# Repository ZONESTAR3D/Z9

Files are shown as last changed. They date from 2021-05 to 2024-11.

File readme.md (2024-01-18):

### :globe_with_meridians: Choose Language (Translated by google)
(https://github-com.translate.goog/ZONESTAR3D/Z9?_x_tr_sl=en&_x_tr_tl=es)
(https://github-com.translate.goog/ZONESTAR3D/Z9?_x_tr_sl=en&_x_tr_tl=pt)
(https://github-com.translate.goog/ZONESTAR3D/Z9?_x_tr_sl=en&_x_tr_tl=fr)
(https://github-com.translate.goog/ZONESTAR3D/Z9?_x_tr_sl=en&_x_tr_tl=de)
(https://github-com.translate.goog/ZONESTAR3D/Z9?_x_tr_sl=en&_x_tr_tl=it)
(https://github-com.translate.goog/ZONESTAR3D/Z9?_x_tr_sl=en&_x_tr_tl=sv)
(https://github-com.translate.goog/ZONESTAR3D/Z9?_x_tr_sl=en&_x_tr_tl=pl)
(https://github-com.translate.goog/ZONESTAR3D/Z9?_x_tr_sl=en&_x_tr_tl=da)
(https://github-com.translate.goog/ZONESTAR3D/Z9?_x_tr_sl=en&_x_tr_tl=cs)
(https://github-com.translate.goog/ZONESTAR3D/Z9?_x_tr_sl=en&_x_tr_tl=hr)
(https://github-com.translate.goog/ZONESTAR3D/Z9?_x_tr_sl=en&_x_tr_tl=ro)
(https://github-com.translate.goog/ZONESTAR3D/Z9?_x_tr_sl=en&_x_tr_tl=sk)

(https://github-com.translate.goog/ZONESTAR3D/Z9?_x_tr_sl=en&_x_tr_tl=ru)
(https://github-com.translate.goog/ZONESTAR3D/Z9?_x_tr_sl=en&_x_tr_tl=ja)
(https://github-com.translate.goog/ZONESTAR3D/Z9?_x_tr_sl=en&_x_tr_tl=ko)
(https://github-com.translate.goog/ZONESTAR3D/Z9?_x_tr_sl=en&_x_tr_tl=id)
(https://github-com.translate.goog/ZONESTAR3D/Z9?_x_tr_sl=en&_x_tr_tl=th)
(https://github-com.translate.goog/ZONESTAR3D/Z9?_x_tr_sl=en&_x_tr_tl=vi)
(https://github-com.translate.goog/ZONESTAR3D/Z9?_x_tr_sl=en&_x_tr_tl=iw)
(https://github-com.translate.goog/ZONESTAR3D/Z9?_x_tr_sl=en&_x_tr_tl=ar)
(https://github-com.translate.goog/ZONESTAR3D/Z9?_x_tr_sl=en&_x_tr_tl=tr)
(https://github-com.translate.goog/ZONESTAR3D/Z9?_x_tr_sl=en&_x_tr_tl=el)
(https://github-com.translate.goog/ZONESTAR3D/Z9?_x_tr_sl=en&_x_tr_tl=pt)
(https://github-com.translate.goog/ZONESTAR3D/Z9?_x_tr_sl=en&_x_tr_tl=zh-CN)

----
### About ZONESTAR Z9 series 3d printer
The main features of Z9 include:  
1. Used **Aluminum profile frame** structure makes the machine  stronger and more stable. The profiles screw is directly fixed, which is more accurate than using profile connectors.  
2. Used **Core-XY** drive structure effectively reduces the weight of the motion system.
3. Used **Open builds pulley + V-profile track**. It has the comprehensive characteristics of high precision, high speed, low resistance and low cost.  
4. **Dule drive z-axis** design is adopted to simplify leveling and improve the stability of the printing platform.  
5. **Elastic replaceable hotend** design is adopted. Fast heat exchange end (extruder) can be selected according to different printing material requirements.   More details, please refer to [**here**](https://github.com/ZONESTAR3D/Upgrade-kit-guide/tree/main/HOTEND)

----
## :file_folder:[Z9V5](https://github.com/ZONESTAR3D/Z9/tree/main/Z9V5)
**Z9V5** is the latest version of Z9 series. Compared with **Z9M4**, the main upgrades include:  
1. Higher pre assembly ratio and faster installation.  
2. The appearance is more beautiful.  
3. Using TMC silent motor drive module, the operation noise is lower (less than 55db @ 1 meter distance).  
4. Upgrade to dual Z driver.  
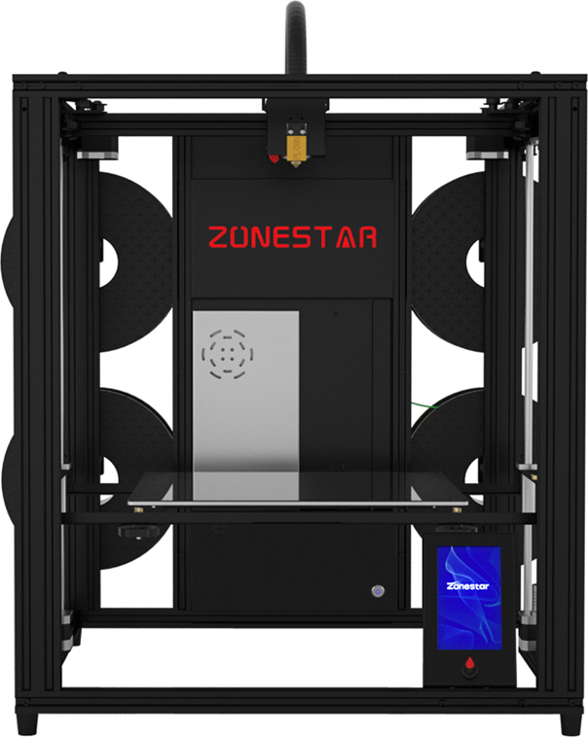
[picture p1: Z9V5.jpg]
Z9V5

#### What's different between Z9V5 with Z9V5Pro    
1. **Z9V5** used 128x64 dots LCD screen (LCD12864) and a PC hotbed film.  
2. **Z9V5Pro** used used a 4.3" TFT-LCD screen (LCD-DWIN) and glass print platform.
  
### [:file_folder:Z9V5-MK1](https://github.com/ZONESTAR3D/Z9/tree/main/Z9V5/Z9V5-MK1) 
**The first version Z9V5**.   

### [:file_folder:Z9V5-MK2](https://github.com/ZONESTAR3D/Z9/tree/main/Z9V5/Z9V5-MK2)
**The 2nd version Z9V5**.   
##### Z9V5-MK2 upgrade than Z9V5-MK1:  
1. **Hot end interface** When shipping, the print head (hotend assembly) is separated from the backplane. There are 5 connectors behind the backplane, which can connect the wiring of the hot end without opening the control box. It will help switch between [**different types of hotends**](https://github.com/ZONESTAR3D/Upgrade-kit-guide/tree/main/HOTEND) quickly.  
2. Improved the M4 hotend from the 2nd version (HM4-V2) to the 3rd version(HM4-V3). More details of the M4 hotend, please refer to [Here](https://github.com/ZONESTAR3D/Upgrade-kit-guide/tree/main/HOTEND/M4%20%204-IN-1-OUT%20Mixing%20Color%20Hotend).  
3. Improved the backlight of ZONESTAR LOGO.  
4. Improved the cover case of control box to make it easier to open.  
5. improved the belt transmission device to prevent the belt from scratching the idler pulley.  
6. improved the filament run out installation to make it solve the problem that may lead to the winding of filament.    
    
### [:file_folder:Z9V5-MK3](https://github.com/ZONESTAR3D/Z9/tree/main/Z9V5/Z9V5-MK3)
**The 3rd version Z9V5**.    
##### **Z9V5-MK3 mainly improves than Z9V5-MK2**:  
1. Upgraded bed leveling sensor to [**ZLSensor**](https://aliexpress.com/item/1005002865311470.html), to replace the PL-08N bed leveling sensor. ZLSensor can probing the glass directly.  
2. Upgraded the extruder motor drivers to [**TMC2225**](https://aliexpress.com/item/1005003270721219.html)(from A4988). So **Z9V5-MK3**'s firmware is different with **Z9V5-MK1** and **Z9V5-MK2**.  

### [:file_folder:Z9V5-MK4](https://github.com/ZONESTAR3D/Z9/tree/main/Z9V5/Z9V5-MK4)
**The 4th version Z9V5**.    
##### **Z9V5-MK4 mainly improves than Z9V5-MK3**:  
1. Use 4-IN-1-OUT non color mixing hotend as default hotend.
2. Use magnetic hot bed sticker to replace hot bed glass.
3. Bed leveling sensor used PL-08N.
4. Optimized structure on top assembly, filament run out sensor case.

### [:file_folder:Z9V5-MK5](https://github.com/ZONESTAR3D/Z9/tree/main/Z9V5/Z9V5-MK5)
**The 5th version Z9V5**.    
##### **Z9V5-MK5 mainly improves than Z9V5-MK4**:  
Used M4V6 (the 6th version 4-IN-1-OUT mix color) hotend as default hotend to replace of the E4 hotend.   

### [:file_folder:Z9V5-MK6](https://github.com/ZONESTAR3D/Z9/tree/main/Z9V5/Z9V5-MK6)
**The 6th version Z9V5**.    
##### **Z9V5-MK6 mainly improves than Z9V5-MK5**:  
1. Upgrade to Dual Gear Extruders (2x BMG left hand and 2x BMG right hand).
2. Upgrade control board to ZM3E4 V3.0.1.    
3. Changed the motor drive modules (4xTMC2208 + 4xA4988).

----
## :file_folder:[Z9M4](./Z9M4/) 
#### [:book:Documents](./Z9M4/readme.md)    
**Z9M4** is a version of Z9 series launched in 2020. Compared with Z9FM3, the main upgrades include:  
1. Upgrade to 4 extruders  
2. Upgrade to 4-IN-1-OUT hotend  
3. Upgrade to 32 bits control board  
**NOTE: Z9M4 is stopped produce since April 2021**  
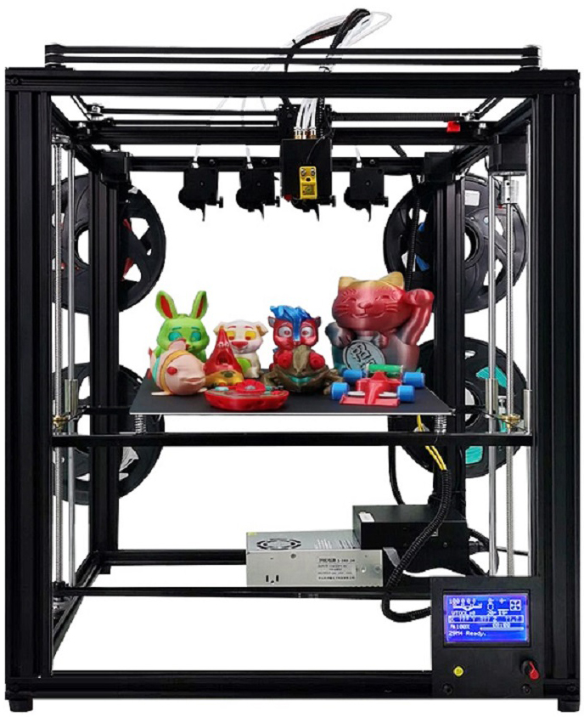
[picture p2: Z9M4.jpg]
Z9M4


----
## :file_folder:[Z9M3](./Z9M4/)  
**Z9M3** is a version of Z9 series launched in 2019.  it has produced two versions, Z9T/Z9F. Compared with Z9M2, the main upgrades include:  
1. Upgrade to 3 extruders  
2. Upgrade to 3-IN-1-OUT hotend  
3. From Z9F, it upgrade the extduer to a Titan extruders.  
**NOTE: Z9M3 is stopped produce since April 2020**  
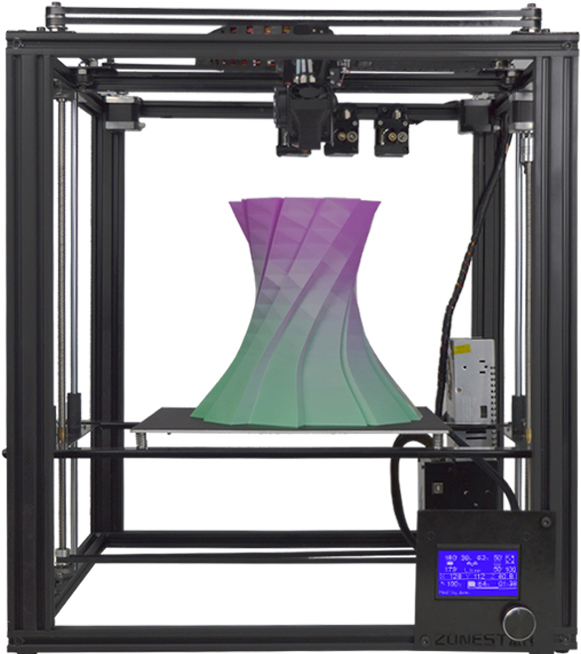
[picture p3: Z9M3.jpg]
Z9FM3
  

----
## Z9M2 
**Z9M2** launched in 2018, it is the first verison of Z9 series. it has produced two versions, Z9 and Z9S. Z9 use a H-BOT structure and Z9S used a Core-XY structure, and after Z9S, all of the Z9 series are used Core-XY structure.

------
### :memo: How to downlod files from Github page?
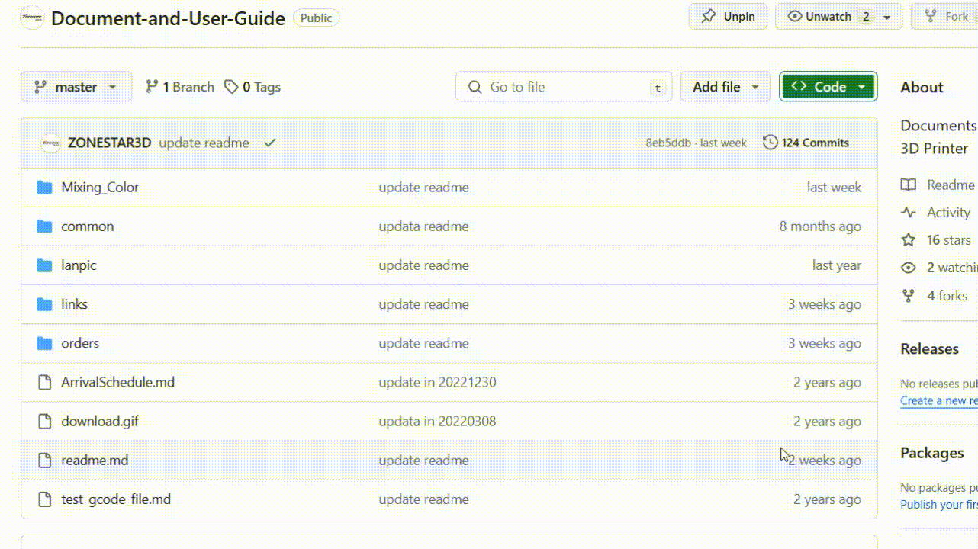
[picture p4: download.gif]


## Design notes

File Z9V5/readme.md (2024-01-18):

# User Guide for ZONESTAR Z9V5 3D Printer 

-----
## Contents
- **[Translate this page](#translate-this-page)**
- **[User Guide links](#link-to-user-guide-for-z9v5pro-3d-printers)**
- **[What's different on Z9V5-MK1/MK2/MK3/MK4/MK5/MK6](#whats-different-on-z9v5-mk1mk2mk3mk4mk5mk6)**
- **[How to distinguish Z9V5-MK1/MK2/MK3/MK4/MK5/MK6](#how-to-distinguish-z9v5-mk1mk2mk3mk4mk5mk6)**
- **[Troubleshooting](#troubleshooting)**

-----
### :globe_with_meridians: Translate this page
We provide online documentation because it is easily translated into a language you are familiar with. Here are some common browser translation plug-ins for your reference.
- [**Windows Edge Translate Add-on**](https://microsoftedge.microsoft.com/addons/detail/edge-translate/bfdogplmndidlpjfhoijckpakkdjkkil?hl=en-US)    
- [**Firefox Translations Add-on**](https://support.mozilla.org/en-US/kb/firefox-translations-add-on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)
- [**Google Translate Chrome Extension**](https://chrome.google.com/webstore/detail/google-translate/aapbdbdomjkkjkaonfhkkikfgjllcleb)

-----
### Link to user guide for Z9V5Pro 3D Printers 
- :file_folder: **Z9V5Pro-MK6: https://github.com/ZONESTAR3D/Z9/tree/main/Z9V5/Z9V5-MK6**    
- :file_folder: **Z9V5Pro-MK5: https://github.com/ZONESTAR3D/Z9/tree/main/Z9V5/Z9V5-MK5**    
- :file_folder: **Z9V5Pro-MK4: https://github.com/ZONESTAR3D/Z9/tree/main/Z9V5/Z9V5-MK4**    
- :file_folder: **Z9V5Pro-MK3: https://github.com/ZONESTAR3D/Z9/tree/main/Z9V5/Z9V5-MK3**    
- :file_folder: **Z9V5Pro-MK2: https://github.com/ZONESTAR3D/Z9/tree/main/Z9V5/Z9V5-MK2**    
- :file_folder: **Z9V5Pro-MK1: https://github.com/ZONESTAR3D/Z9/tree/main/Z9V5/Z9V5-MK1**    

-----
### What's different on Z9V5-MK1/MK2/MK3/MK4/MK5/MK6
#### :black_circle: Z9V5-MK6 mainly improves than Z9V5-MK5:       
1. Upgraded to Dual Gear Extruders.
2. Upgraded control board to ZM3E4 V3.     
3. Changed motor drivers: TMC2208 used on driving XYZ motors and A4988 used on driving extrurder motors.     
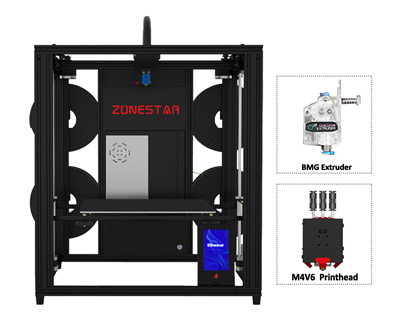
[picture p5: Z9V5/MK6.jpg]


#### :black_circle: Z9V5-MK5 mainly improves than Z9V5-MK4:     
Used M4V6 (the 6th version 4-IN-1-OUT mix color) hotend as default hotend.   
**[What's different between M4V6 hotend and E4 hotend][FAQ_M4E4].**     
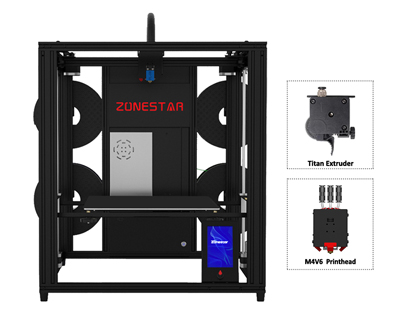
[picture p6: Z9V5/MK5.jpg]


#### :black_circle: Z9V5-MK4 mainly improves than Z9V5-MK3:  
1. Use E4 (4-IN-1-OUT non mix color) hotend as default hotend.
2. Use flexibel magnetic hot bed sticker to replace hot bed glass.
3. Bed leveling sensor used PL-08N.
4. Optimized structure on top assembly, filament run out sensor case, etc..    
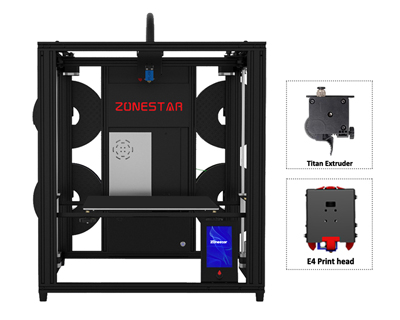
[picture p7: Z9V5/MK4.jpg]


#### :black_circle: Z9V5-MK3 mainly improves than Z9V5-MK2:
1. Upgraded bed leveling sensor to [**ZLSensor**](https://aliexpress.com/item/1005002865311470.html) from [**PL-08N**](https://www.aliexpress.com/item/2255800409994958.html), ZL-Sensor can probing the glass directly.  
2. Changed motor drivers: TMC2225 used on driving XYZ motors and extrurder motors..     
3. Upgraded the M4 hotend from the 3nd version (***M4V3***) to the 4th version(***M4V4***).      
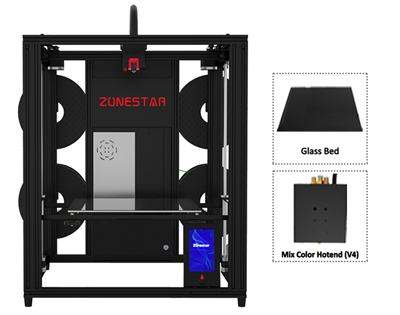
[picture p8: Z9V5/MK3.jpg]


#### :black_circle: Z9V5-MK2 mainly improves than Z9V5-MK1:    
1. Added air connectors for hot end wiring, making it easier to switch between different types of hot ends.
2. Upgraded the M4 hotend from the 2nd version (***M4V2***) to the 3rd version(***M4V3***). .  
3. Improved the backlight of ZONESTAR LOGO.  
4. Improved the cover case of control box to make it easier to open.  
5. improved the belt transmission device to prevent the belt from scratching the idler pulley.  
6. improved the filament run out installation.    
:warning: **NOTE** :warning:   
Due to the shortage of chips, a small numbers of **Z9V5-MK2** used **ZM3E4V1** control board. Please check the product serial number (a white lable pasted on the power supply). If the product with serial number **V1xxxxxxxx** , it means your machine used a **ZM3E4V1** control board. Basically ZM3E4V1 has the same features with ZM3E4V2.        
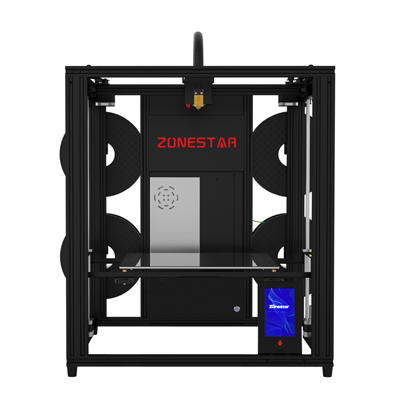
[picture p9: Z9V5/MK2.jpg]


#### :black_circle: Z9V5-MK1 is the first version Z9V5    

-----
### How to distinguish Z9V5-MK1/MK2/MK3/MK4/MK5/MK6
You can distinguish MK1/MK2/MK3/MK4 by product serial number. There is a white sticker on the power supply, which indicates the product serial number.  

- **Z9V5-MK1:** Serial Number is **xxxxxxxxxx**   
- **Z9V5-MK2:** Serial Number is **V1-xxxxxxxxxx** and **V2-xxxxxxxxxx**    
- **Z9V5-MK3:** Serial Number is **MK3-xxxxxxxxxx**  
- **Z9V5-MK4:** Serial Number is **MK4-xxxxxxxxxx**  
- **Z9V5-MK5:** Serial Number is **MK5-xxxxxxxxxx**  
- **Z9V5-MK6:** Serial Number is **MK6-xxxxxxxxxx**  

-----
### Troubleshooting
If you have any problem when installing and using Z9V5, please read the [**:book: Z9V5Pro Troubleshooting**][Troubleshooting] to find a solution a solution first.

-----
### :memo: How to downlod files from Github page?
   

-----
[FAQ_M4E4]: https://github.com/ZONESTAR3D/Upgrade-kit-guide/blob/main/HOTEND/FAQ_M4E4.md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
[Troubleshooting]: https://github.com/ZONESTAR3D/Z9/tree/main/Z9V5/Z9V5_FAQ

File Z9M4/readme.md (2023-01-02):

### :globe_with_meridians: Choose Language (Translated by google)
(https://github-com.translate.goog/ZONESTAR3D/Z9/tree/main/Z9M4?_x_tr_sl=en&_x_tr_tl=es)
(https://github-com.translate.goog/ZONESTAR3D/Z9/tree/main/Z9M4?_x_tr_sl=en&_x_tr_tl=fr)
(https://github-com.translate.goog/ZONESTAR3D/Z9/tree/main/Z9M4?_x_tr_sl=en&_x_tr_tl=pt)
(https://github-com.translate.goog/ZONESTAR3D/Z9/tree/main/Z9M4?_x_tr_sl=en&_x_tr_tl=de)
(https://github-com.translate.goog/ZONESTAR3D/Z9/tree/main/Z9M4?_x_tr_sl=en&_x_tr_tl=it)
(https://github-com.translate.goog/ZONESTAR3D/Z9/tree/main/Z9M4?_x_tr_sl=en&_x_tr_tl=pl)
(https://github-com.translate.goog/ZONESTAR3D/Z9/tree/main/Z9M4?_x_tr_sl=en&_x_tr_tl=ru)
(https://github-com.translate.goog/ZONESTAR3D/Z9/tree/main/Z9M4?_x_tr_sl=en&_x_tr_tl=pt)
(https://github-com.translate.goog/ZONESTAR3D/Z9/tree/main/Z9M4?_x_tr_sl=en&_x_tr_tl=el)

(https://github-com.translate.goog/ZONESTAR3D/Z9/tree/main/Z9M4?_x_tr_sl=en&_x_tr_tl=ja)
(https://github-com.translate.goog/ZONESTAR3D/Z9/tree/main/Z9M4?_x_tr_sl=en&_x_tr_tl=ko)
(https://github-com.translate.goog/ZONESTAR3D/Z9/tree/main/Z9M4?_x_tr_sl=en&_x_tr_tl=id)
(https://github-com.translate.goog/ZONESTAR3D/Z9/tree/main/Z9M4?_x_tr_sl=en&_x_tr_tl=th)
(https://github-com.translate.goog/ZONESTAR3D/Z9/tree/main/Z9M4?_x_tr_sl=en&_x_tr_tl=vi)
(https://github-com.translate.goog/ZONESTAR3D/Z9/tree/main/Z9M4?_x_tr_sl=en&_x_tr_tl=iw)
(https://github-com.translate.goog/ZONESTAR3D/Z9/tree/main/Z9M4?_x_tr_sl=en&_x_tr_tl=ar)
(https://github-com.translate.goog/ZONESTAR3D/Z9/tree/main/Z9M4?_x_tr_sl=en&_x_tr_tl=tr)
(https://github-com.translate.goog/ZONESTAR3D/Z9/tree/main/Z9M4?_x_tr_sl=en&_x_tr_tl=zh-CN)
----------
## NOTICE
### Before using the 3d printer, please:  
1. Carefully to read the pages (from 54~56) in the "1. User Guide\Z9M4 user guide".  
2. Carefully to read the file "1. User Guide\Mix Color HOTEND User Guide - load and unload filament.pdf".  
3. Carefully to read "1. User Guide\Operature guide for Mixing Color Printer.pdf"  
***ATTETION: Incorrect filament loading may cause to clog the hotend, if the hotend is clogged, please refer to the document "4. TroubleShootings\How to clean the cloged mixing color hotend.pdf" to fix***  

## Download Z9M4 files
[**Download all the Z9M4 files in one go**](https://downgit.github.io/#/home?url=https:%2F%2Fgithub.com%2FZONESTAR3D%2FZ9%2Ftree%2Fmain%2FZ9M4)     
**If it doesn't work, please refer to** [**here**](https://stackoverflow.com/questions/7106012/download-a-single-folder-or-directory-from-a-github-repo)     
   
# Documents
## 1. User Guide 
**Included:**  
1. Installation and quick user guide  
2. LCD screen menu description  
3. Installation video tutorial  
4. Operature guide for mixing color printer    

## 2. Operation Guide
**Included:**  
1. USB driver  
2. Host Software - Print from PC guide  
3. Advanced features guide  
4. Bed auto leveling feature guide  

## 3. Slicing
**Included slicing guide, for the newest slicing guide, please click here [slicing guide](https://github.com/ZONESTAR3D/Slicing-Guide)**

## 4. Test gcode
**Included some testing gcode files**  

## 5. TroubleShootings
**Included troubleshooting and FAQ files**

## 6. Print Parts
**Parts stl files for this kit**   

## 7. Firmware
- [**Firmware bin file**](https://github.com/ZONESTAR3D/Firmware/tree/master/Z9/Z9M4)  
- [**Firmware source code** ](https://github.com/ZONESTAR3D/source-code-for-3d-printer)

## Video tutorial  
**NOTE: The video tutorial may be a little different with your machine because of firmware version is different, for reference only**     
### Installation and operation      
- [***How to load filament (one color)***](https://youtu.be/W1_XiT4g9kg)  
- [***How to load filament (Mutli-colors)***](https://youtu.be/Rsd8GYrEVCQ)  
- [***Bed Leveling***](https://youtu.be/lgYZA-pzMsM)    
- [***Gradient Mixing Color Printing***](https://youtu.be/agj3J1HBDt8)    
- [***Random Mixing Color Printing***](https://youtu.be/qvT_BX4C2Rk)  

### Advanced features
- [***Auto Retract Feature***](https://youtu.be/4HVIGxZfM80)  
- [***Filament Runout***](https://youtu.be/viTvzIskwY8)  

### Slicing guide (by Cura)  
- [***Install and setup Cura***](https://youtu.be/h2GynyUo7wQ)    
- [***slicing 1 color 3d object***](https://youtu.be/UDgjGRFrELc)    
- [***slicing 4 colors 3d object***](https://youtu.be/hP6Socp-Cz0)     
- [***slicing 8 colors 3d object***](https://youtu.be/qQ6UnTysqK0)          

# Z9 upgrade kit / parts
## Laser engine
By upgrading this item, you can turn your 3D printer into a simple laser engraving machine. Higher power laser modules can improve engraving speed or support materials with higher melting point.  
- [**User guide**](https://github.com/ZONESTAR3D/Upgrade-kit-guide/tree/main/Laser%20Engraving)  
- [**Sell link**](https://www.aliexpress.com/item/4001309902136.html)  
## WiFi
By upgrading this item, you can remote control your 3d printer.    
- [**User guide**](https://github.com/ZONESTAR3D/Upgrade-kit-guide/tree/main/WiFi)  
- [**Sell link**](https://www.aliexpress.com/item/1005002378551489.html)  
## Direct drive extruder
By upgrading this project, you can print flexible materials (such as TPU filament). Of course, it also has other advantages and disadvantages of the "direct drive" extruders, such as having less strings issue, better flow, more supporting materials, etc., Also because of the heavier weight of the extruder, the printing speed must be lower.  
- [**User guide**](https://github.com/ZONESTAR3D/Upgrade-kit-guide/tree/main/Direct%20Drive%20Extrruder)   
- [**Sell link**](https://www.aliexpress.com/item/1005002847644867.html)   
## Hotends
Each type of hot end has its advantages and disadvantages, you can choose different hotends according to different requirement:    
- **High-speed and high-temperature Hotend (single color)**: It can support higher  printing speed and higher temperature consumables (up to 300 degrees when using stainless steel nozzles), and can be used to print PVC and PC.  
- **3-IN-3-OUT Hotend**: It can support printing different typs of filaments in one 3d prints, such as PLA+PVA.  
- **3-IN-2-OUT Hotend**: It can be regarded as a combination of 2-IN-1-OUT and a single-color hot end, which can simultaneously achieve the needs of color mixing and printing of different materials.    
We will launch more hot ends in the future, so stay tuned. If you have any suggestions, please don't hesitate to let us know at any time.   
- [**User guide**](https://github.com/ZONESTAR3D/Upgrade-kit-guide/tree/main/HOTEND)   
- [**4-IN-1-OUT Non-Mixing hotend**](https://www.aliexpress.com/item/1005002951777699.html)   
- [**High Speed Printing hotend**](https://www.aliexpress.com/item/1005002829919346.html)  
- [**3-IN-1-OUT hotend**](https://www.aliexpress.com/item/1005001275429959.html)
- [**3-IN-2-OUT hotend**](https://www.aliexpress.com/item/1005001275429959.html)
- [**3-IN-3-OUT hotend**](https://www.aliexpress.com/item/1005001275429959.html)
## Bed leveling sensor
- [**User guide**](https://github.com/ZONESTAR3D/Upgrade-kit-guide/tree/main/Bed%20Leveling%20Sensor)    
- [**ZLSensor**](https://www.aliexpress.com/item/1005002865311470.html)  
- [**3DTouch**](https://www.aliexpress.com/item/1005001464420529.html)

## How to downlod files from Github page
#### Step 1: Click this link [**https://downgit.github.io/**](https://downgit.github.io/) 
#### Step 2: Copy the Github file or direcotry link which you want to download.
#### Step 3: Click download button and wait a few seconds, it will start to download automatically. 


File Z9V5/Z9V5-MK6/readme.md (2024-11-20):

[M4V6_PRECAUTION]: https://github.com/ZONESTAR3D/Upgrade-kit-guide/blob/main/HOTEND/M4/M4_V6/M4V6_Precaution.md
[Z9V5MK6_STEPBYSTEP]: https://github.com/ZONESTAR3D/Z9/blob/main/Z9V5/Z9V5-MK6/step_by_step.md
[Z9V5MK6_LOADFILAMENT]: https://github.com/ZONESTAR3D/Z9/blob/main/Z9V5/Z9V5-MK6/2.Operation/Operation.md#load-filaments
[Z9V5MK6_OPTION]: https://github.com/ZONESTAR3D/Z9/blob/main/Z9V5/Z9V5-MK6/OptionalFeatures.md
[LINK_M4V6]: https://github.com/ZONESTAR3D/Upgrade-kit-guide/blob/main/HOTEND/M4/M4_V6
[LINK_MIX_FEATURE]: https://github.com/ZONESTAR3D/Document-and-User-Guide/blob/master/Mixing_Color
[LINK_FIRMWARE]: https://github.com/ZONESTAR3D/Firmware/blob/master/Z9/Z9V5/bin/Z9V5Pro-MK6
[LINK_SOURCECODE]: https://github.com/ZONESTAR3D/source-code-for-3d-printer
[LINK_TROUBLESHOOTING]: https://github.com/ZONESTAR3D/Z9/blob/main/Z9V5/Z9V5_FAQ
[M4_TEST_GCODE]: https://github.com/ZONESTAR3D/Slicing-Guide/blob/master/PrusaSlicer/test_gcode/M4/readme.md
[GCODE_REF1]: https://beginner3dprinting.com/what-is-g-code-in-3d-printing/
[GCODE_REF2]: https://www.reprap.org/wiki/G-code

----
## <a id="choose-language">:globe_with_meridians: Choose language </a>










----
# User Guide for ZONESTAR Z9V5Pro-MK6 3D Printer 
### [:arrow_down: Download All Document](https://downgit.github.io/#/home?url=https://github.com/ZONESTAR3D/Z9/tree/main/Z9V5/FZ9V5-MK6) 

----
## :warning: ATTENTION PLEASE
#### :loudspeaker: Before using the machine, please read [:book:"Precautions for using M4V6"][M4V6_PRECAUTION] carefully.
#### :loudspeaker: Must load 4 filaments onto the M4V6 hotend simultaneously, incorrect operationa may block the mix color hotend. If the hot end blockage caused by incorrect operation, it is not covered by the warranty. For how to load filaments, please refer to [:book: this guide][Z9V5MK6_LOADFILAMENT].
#### :loudspeaker: If you are a beginner of 3d printer, please carefully read the [:book: Step-by-Step Guide][Z9V5MK6_STEPBYSTEP], and following the steps to do.   
- [:book: **Precautions for using M4V6**][M4V6_PRECAUTION]
- [:book: **How to load filaments correctly**][Z9V5MK6_LOADFILAMENT]
- [:book: **Step-by-Step Guide**][Z9V5MK6_STEPBYSTEP] 

------
## :book: Contents
- [**Installation guide**](#a1)  
- [**Operation guide**](#a2)  
- [**Test gcode files**](#a3)
- [**Slicing software**](#a4)
- [**Firmware**](#a5)
- [**Troubleshootings**](#a6)
- [**Print parts stl files**](#a7)
- [**Optional upgrade features**](#a8)

-----
## <a id="a1"> 1. Installation guide </a>
First, please refer to the following documents and videos to complete the installation and wiring of the machine.
### Installation   
- [:book: Installation Guide Online Document](./1.Installation/Installation.md) 
- [:blue_book: Installation Guide PDF file](./1.Installation/Installation.pdf) 
- [:clapper: Installation Guide Video tutorial](https://youtu.be/TGHUVzV1Pg4)   
### Wiring    
- [:book: Wiring Guide Online Document](./1.Installation/Wiring.md) 
- [:blue_book: Wiring Guide PDF file](./1.Installation/Wiring.pdf) 
- [:art: Wiring diagram](./1.Installation/Z9V5Pro_Wiring_Diagram.jpg) 
- [:clapper: Wiring Video tutorial](https://youtu.be/tQQNLDOpdQU)

## <a id="a2"> 2. Operation Guide </a>
### **Introduction to LCD Control Panel**     
After completing the installation and wiring, please take a look the below guide to know how to use the control panel (LCD Screen), and understand the functions of LCD menu generally.      
- [:book: LCD Menu Online Document](./2.Operation/LCDMENU_Description.md)    
- [:blue_book: LCD Menu PDF file](./2.Operation/LCDMENU_Description.pdf)    
#### **Print your first works**     
Now you can try to print your "Hello word" works, before starting printing, you first need to make a simple correction to the height of the hot bed (it is called "bed leveling"), and then load the filaments into the extruder (please note that regardless of the color of your print, you need to load all 4 filaments into the extruders and hot end). Next, you can insert the SD card into the machine and choose a testing 3D model gcode file in the SD card. For details, please refer to the documents below.     
- [:book: Operation Guide Online Document](./2.Operation/Operation.md) 
- [:blue_book: Operation Guide PDF file](./2.Operation/Operation.pdf) 
#### :page_with_curl: More features
You can also read the following documents to gain a deeper understanding of the extruder (hot end and print head) used by your machine, as well as some advanced features of the machine.      
- [:book: Mix color feature use guide][LINK_MIX_FEATURE]     
- [:book: M4V6 Hotend introduction][LINK_M4V6] 
- [:book: Print From PC](./2.Operation/PrintFromPC/readme.md)   
- [:book: Advance features use guide](./2.Operation/Advance_Features.md)    

## <a id="a3"> 3. Test G-code file </a>
**:pencil: What Is G-code In 3D Printing?**    
G-code is information, or instructions that 3d printer requires in order to print a 3 dimensional object, it is the langurage of the 3d printer can understand. G-Code is generated by your slicing software, by translating a standard 3D modelling file such as STL, object, AMF file etc..  :page_with_curl: [**Reference 1**][GCODE_REF1]  :page_with_curl: [**Reference 2**][GCODE_REF2]      
We stored some test gcode files in SD card, to help verify whether the machine was working properly or to demonstrate what printing functions this machine has. If you can't find the test gcode files in the SD card, please download from [:arrow_down: **here**](./3.TestGcode/Test_gcode.zip).
- **xyz_cube.gcode**: A simple test gcode file used to verify if the machine was working well.  
- **dog.gcode**: A classic printing quality test file. 
- **Vase.gcode**: A test vase.      
  - **GradientMix_Vase.gcode**: A vase as the same with vase.gcode but enabled "gradient mix" feature.
  - **RandomMix_Vase.gcode**: A vase as the same with vase.gcode but enabled "random mix" feature.
- **M4_4CTest.gcode**: A base 4 colors test file for 3d printer with a M4 hot end.
- **M4_4C_BODY3D.gcode**: A biger 4 color test file.   
- **16color_tower.gcode**: A base 16 color test file to show the result of mixed different color filaments. 
- **level_test_310.gcode**: A test file used to verify the Hot bed flatness (without bed auto leveling). 
- **level_test_310-G29.gcode**: A test file used to verify the Hot bed flatness (with bed auto leveling).     
**[:arrow_down: Download more test gcode files][M4_TEST_GCODE].**
 
## <a id="a4"> 4. Slicing </a>
**[:pencil: What is slicing In 3D Printing?](https://en.wikipedia.org/wiki/Slicer_(3D_printing))**             
A slicer is toolpath generation software used in the majority of 3D printing processes for the conversion of a 3D object model to specific instructions for the printer. In particular, the conversion from a model in STL format to printer commands in g-code format in fused filament fabrication and other similar processes.   
- [:book:Slicer User Guide Online Document](./4.Slicing/readme.md)    
- [:blue_book: Slicer User Guide PDF File](./4.Slicing/Slicing.pdf)   

## <a id="a5"> 5. Firmware </a>
**:pencil: What is firmware bin file and source code?**    
Firmware bin file is the exact memory that is written to the embedded flash.        
Firmware source code is the core part of the firmware. Our firmware source code is base on [**marlin**](https://www.marlinfw.org).  
You can download firmware bin file or source code from the below link.  
- [:arrow_down: Firmware bin file][LINK_FIRMWARE]   
- [:arrow_down: Firmware source code][LINK_SOURCECODE]     

## <a id="a6"> 6. Troubleshooting </a>
If you have any problems installing and using the printer, please try to find a solution from the [:book: Troubleshooting Online Document][LINK_TROUBLESHOOTING] first. If you cannot solve this problem, please contact us by email (:email: support@zonestar3d.com).      

## <a id="a7"> 7. Print Parts </a>
There are several components on the machine that are printed, and we have also prepared some upgrades for you. If you like, you can download and print them and then install them on your machine.

-----
## <a id="a8"> Optional features </a>
We have introduced some optional features for this machine, you can upgrade these features at any time according to your preferences. If you are interesting in this, please read Optional upgrade features guide to get more detailed information.
- [:book: Optional upgrade features guide online document][Z9V5MK6_OPTION]
- [:blue_book: Optional upgrade features guide pdf file](./OptionalFeatures.pdf)

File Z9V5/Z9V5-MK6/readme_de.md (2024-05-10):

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

----
## <a id="choose-language">:globe_with_meridians: Choose language </a>










----
# Benutzerhandbuch für den ZONESTAR Z9V5Pro-MK6 3D-Drucker

----
## :warning: BITTE ACHTUNG
#### :loudspeaker: Bevor Sie das Gerät verwenden, lesen Sie bitte [:book:"Vorsichtsmaßnahmen für die Verwendung von M4V6"][M4V6_PRECAUTION] sorgfältig durch.
#### :loudspeaker: Es müssen 4 Filamente gleichzeitig auf das M4V6-Hotend geladen werden. Bei falscher Bedienung kann das Mischfarben-Hotend blockiert werden. Wenn die Blockierung des heißen Endes auf eine fehlerhafte Bedienung zurückzuführen ist, fällt sie nicht unter die Garantie. Informationen zum Laden von Filamenten finden Sie in [:book: dieser Anleitung][Z9V5MK6_LOADFILAMENT].
#### :loudspeaker: Wenn Sie ein Anfänger im Umgang mit 3D-Druckern sind, lesen Sie bitte sorgfältig die [:book: Schritt-für-Schritt-Anleitung][Z9V5MK6_STEPBYSTEP] und befolgen Sie die erforderlichen Schritte.
- [:book: **Vorsichtsmaßnahmen für die Verwendung von M4V6**][M4V6_PRECAUTION]
- [:book: **So laden Sie Filamente richtig**][Z9V5MK6_LOADFILAMENT]
- [:book: **Schritt-für-Schritt-Anleitung**][Z9V5MK6_STEPBYSTEP]

------
## :book: Inhalt
- [**Installationsanleitung**](#a1)
- [**Bedienungsanleitung**](#a2)
- [**Gcode-Dateien testen**](#a3)
- [**Slicing-Software**](#a4)
- [**Firmware**](#a5)
- [**Fehlerbehebung**](#a6)
- [**Teile-STL-Dateien drucken**](#a7)
- [**Optionale Upgrade-Funktionen**](#a8)

-----
## <a id="a1"> 1. Installationsanleitung </a>
Bitte beachten Sie zunächst die folgenden Dokumente und Videos, um die Installation und Verkabelung der Maschine abzuschließen.
### Installation
- [:book: Installationshandbuch Online-Dokument](./1.Installation/Installation.md)
- [:blue_book: Installationsanleitung PDF-Datei](./1.Installation/Installation.pdf)
- [:clapper: Installationsanleitung, Video-Tutorial](https://youtu.be/TGHUVzV1Pg4)
### Verkabelung
- [:book: Wiring Guide Online Document](./1.Installation/Wiring.md)
- [:blue_book: Verkabelungsanleitung PDF-Datei](./1.Installation/Wiring.pdf)
- [:art: Schaltplan](./1.Installation/Z9V5Pro_Wiring_Diagram.jpg)
- [:clapper: Video-Tutorial zur Verkabelung](https://youtu.be/tQQNLDOpdQU)

## <a id="a2"> 2. Bedienungsanleitung </a>
### **Einführung in das LCD-Bedienfeld**
Nachdem Sie die Installation und Verkabelung abgeschlossen haben, sehen Sie sich bitte die folgende Anleitung an, um zu erfahren, wie Sie das Bedienfeld (LCD-Bildschirm) verwenden und die Funktionen des LCD-Menüs im Allgemeinen verstehen.
- [:book: LCD Menu Online Document](./2.Operation/LCDMENU_Description.md)
- [:blue_book: LCD-Menü-PDF-Datei](./2.Operation/LCDMENU_Description.pdf)
#### **Drucken Sie Ihre ersten Werke**
Jetzt können Sie versuchen, Ihre „Hallo Wort“-Werke zu drucken. Bevor Sie mit dem Drucken beginnen, müssen Sie zunächst eine einfache Korrektur der Höhe des heißen Betts vornehmen (dies wird als „Bettnivellierung“ bezeichnet) und dann die Filamente in den Extruder laden (Bitte beachten Sie, dass Sie unabhängig von der Farbe Ihres Drucks alle 4 Filamente in die Extruder und das Hot-End laden müssen.) Als Nächstes können Sie die SD-Karte in das Gerät einlegen und auf der SD-Karte eine zu testende 3D-Modell-Gcode-Datei auswählen. Einzelheiten entnehmen Sie bitte den untenstehenden Dokumenten.   
- [:book: Operation Guide Online Document](./2.Operation/Operation.md)
- [:blue_book: Bedienungsanleitung im PDF-Format](./2.Operation/Operation.pdf)
#### :page_with_curl: Weitere Funktionen
Sie können auch die folgenden Dokumente lesen, um ein tieferes Verständnis des von Ihrem Gerät verwendeten Extruders (Hot-End und Druckkopf) sowie einiger erweiterter Funktionen des Geräts zu erlangen.  
- [:book: Anleitung zur Verwendung der Farbmischungsfunktion][LINK_MIX_FEATURE]
- [:Buch: M4V6 Hotend-Einführung][LINK_M4V6]
- [:book: Drucken vom PC](./2.Operation/PrintFromPC/readme.md)
- [:book: Gebrauchsanleitung für erweiterte Funktionen](./2.Operation/Advance_Features.md)

## <a id="a3"> 3. G-Code-Datei testen </a>
**:pencil: Was ist G-Code im 3D-Druck?**
Bei G-Code handelt es sich um Informationen oder Anweisungen, die ein 3D-Drucker benötigt, um ein dreidimensionales Objekt zu drucken. Dabei handelt es sich um die Sprache, die der 3D-Drucker verstehen kann. G-Code wird von Ihrer Slicing-Software generiert, indem eine Standard-3D-Modellierungsdatei wie STL, Objekt, AMF-Datei usw. übersetzt wird. :page_with_curl: [**Referenz 1**][GCODE_REF1] :page_with_curl: [**Referenz 2 **][GCODE_REF2]
Wir haben einige Test-Gcode-Dateien auf der SD-Karte gespeichert, um zu überprüfen, ob das Gerät ordnungsgemäß funktioniert, oder um zu demonstrieren, über welche Druckfunktionen dieses Gerät verfügt. Wenn Sie die Test-Gcode-Dateien nicht auf der SD-Karte finden können, laden Sie sie bitte von [:arrow_down: **hier**](./3.TestGcode/Test_gcode.zip) herunter.
- **xyz_cube.gcode**: Eine einfache Test-Gcode-Datei, mit der überprüft wird, ob die Maschine ordnungsgemäß funktioniert.
- **dog.gcode**: Eine klassische Druckqualitätstestdatei.
- **Vase.gcode**: Eine Testvase.
   - **GradientMix_Vase.gcode**: Eine Vase wie bei vase.gcode, aber mit aktivierter Funktion „Gradientenmix“.
   - **RandomMix_Vase.gcode**: Eine Vase wie bei vase.gcode, aber mit aktivierter Funktion „Zufallsmischung“.
- **M4_4CTest.gcode**: Eine Basis-4-Farben-Testdatei für 3D-Drucker mit einem M4-Hot-End.
- **M4_4C_BODY3D.gcode**: Eine größere 4-Farben-Testdatei.
- **16color_tower.gcode**: Eine Basis-16-Farbtestdatei, um das Ergebnis gemischter Filamente unterschiedlicher Farbe anzuzeigen.
- **level_test_310.gcode**: Eine Testdatei zur Überprüfung der Ebenheit des Hot-Bettes (ohne automatische Bettnivellierung).
- **level_test_310-G29.gcode**: Eine Testdatei zur Überprüfung der Ebenheit des Hot-Bettes (mit automatischer Bettnivellierung).
**[:arrow_down: Weitere Test-Gcode-Dateien herunterladen][M4_TEST_GCODE].**
 
## <a id="a4"> 4. Schneiden </a>
**[:pencil: Was ist Schneiden im 3D-Druck?](https://en.wikipedia.org/wiki/Slicer_(3D_printing))**
Ein Slicer ist eine Software zur Werkzeugweggenerierung, die in den meisten 3D-Druckverfahren zur Konvertierung eines 3D-Objektmodells in spezifische Anweisungen für den Drucker verwendet wird. Insbesondere die Konvertierung von einem Modell im STL-Format in Druckerbefehle im G-Code-Format bei der Herstellung von geschmolzenem Filament und anderen ähnlichen Prozessen.
- [:book:Slicer User Guide Online Document](./4.Slicing/readme.md)
- [:blue_book: Slicer-Benutzerhandbuch im PDF-Format](./4.Slicing/Slicing.pdf)

## <a id="a5"> 5. Firmware </a>
**:pencil: Was ist Firmware-Bin-Datei und Quellcode?**
Die Firmware-Bin-Datei ist der genaue Speicher, der in den eingebetteten Flash geschrieben wird.
Der Firmware-Quellcode ist der Kernbestandteil der Firmware. Unser Firmware-Quellcode basiert auf [**marlin**](https://www.marlinfw.org).
Sie können die Firmware-Bin-Datei oder den Quellcode über den folgenden Link herunterladen.
- [:arrow_down: Firmware-Bin-Datei][LINK_FIRMWARE]
- [:arrow_down: Firmware-Quellcode][LINK_SOURCECODE]

## <a id="a6"> 6. Fehlerbehebung </a>
Wenn Sie Probleme bei der Installation und Verwendung des Druckers haben, versuchen Sie bitte zunächst, eine Lösung im [:book: Online-Dokument zur Fehlerbehebung][LINK_TROUBLESHOOTING] zu finden. Wenn Sie dieses Problem nicht lösen können, kontaktieren Sie uns bitte per E-Mail (:email: support@zonestar3d.com).

## <a id="a7"> 7. Teile drucken </a>
Es gibt mehrere Komponenten der Maschine, die gedruckt werden, und wir haben auch einige Upgrades für Sie vorbereitet. Wenn Sie möchten, können Sie sie herunterladen, ausdrucken und dann auf Ihrem Computer installieren.

-----
## <a id="a8">Optionale Funktionen </a>
Wir haben einige optionale Funktionen für dieses Gerät eingeführt. Sie können diese Funktionen jederzeit nach Ihren Wünschen aktualisieren. Wenn Sie daran interessiert sind, lesen Sie bitte den Leitfaden zu optionalen Upgrade-Funktionen, um detailliertere Informationen zu erhalten.
- [:book: Leitfaden für optionale Upgrade-Funktionen, Online-Dokument][Z9V5MK6_OPTION]
- [:blue_book: Leitfaden für optionale Upgrade-Funktionen, PDF-Datei](./OptionalFeatures.pdf)

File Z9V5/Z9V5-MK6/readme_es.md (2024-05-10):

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

----
## <a id="choose-language">:globe_with_meridians: Choose language </a>










----
# Guía del usuario para la impresora 3D ZONESTAR Z9V5Pro-MK6

----
## :warning: ATENCIÓN POR FAVOR
#### loudspeaker: Antes de utilizar la máquina, lea atentamente [:book:"Precauciones para el uso de M4V6"][M4V6_PRECAUTION].
#### loudspeaker: Debe cargar 4 filamentos en el hotend M4V6 simultáneamente, el funcionamiento incorrecto puede bloquear el hotend de mezcla de colores. Si el bloqueo del extremo caliente es causado por una operación incorrecta, no está cubierto por la garantía. Para saber cómo cargar filamentos, consulte [:book: esta guía][Z9V5MK6_LOADFILAMENT].
#### loudspeaker: Si es principiante en el uso de impresoras 3D, lea atentamente la [Guía paso a paso] [Z9V5MK6_STEPBYSTEP] y siga los pasos a seguir.
- [:book: **Precauciones al usar M4V6**][M4V6_PRECAUTION]
- [:book: **Cómo cargar filamentos correctamente**][Z9V5MK6_LOADFILAMENT]
- [:book: **Guía paso a paso**][Z9V5MK6_STEPBYSTEP]
<!-- - [:blue_book: Archivo PDF de la guía paso a paso](./step_by_step.pdf) -->

------
## :book: Contenido
- [**Guía de instalación**](#a1)
- [**Guía de operación**](#a2)
- [**Probar archivos gcode**](#a3)
- [**Software de corte**](#a4)
- [**Firmware**](#a5)
- [**Solución de problemas**](#a6)
- [**Imprimir archivos stl de piezas**](#a7)
- [**Funciones de actualización opcionales**](#a8)

-----
## <a id="a1"> 1. Guía de instalación </a>
Primero, consulte los siguientes documentos y vídeos para completar la instalación y el cableado de la máquina.
### Instalación
- [:book: Documento en línea de la guía de instalación](./1.Installation/Installation.md)
- [:blue_book: archivo PDF de la guía de instalación](./1.Installation/Installation.pdf)
- [:clapper: Videotutorial de la guía de instalación](https://youtu.be/TGHUVzV1Pg4)
### Alambrado
- [:book: Documento en línea de la guía de cableado](./1.Installation/Wiring.md)
- [:blue_book: Archivo PDF de la guía de cableado](./1.Installation/Wiring.pdf)
- [:art: Diagrama de cableado](./1.Installation/Z9V5Pro_Wiring_Diagram.jpg)
- [:clapper: Videotutorial de cableado](https://youtu.be/tQQNLDOpdQU)

## <a id="a2"> 2. Guía de operación </a>
### **Introducción al panel de control LCD**
Después de completar la instalación y el cableado, consulte la siguiente guía para saber cómo utilizar el panel de control (pantalla LCD) y comprender las funciones del menú LCD en general.
- [:book: Documento en línea del menú LCD](./2.Operation/LCDMENU_Description.md)
- [:blue_book: archivo PDF del menú LCD](./2.Operation/LCDMENU_Description.pdf)
#### **Imprime tus primeros trabajos**
Ahora puedes intentar imprimir tus trabajos de "Hola palabra", antes de comenzar a imprimir, primero debes hacer una simple corrección a la altura de la cama caliente (se llama "nivelación de la cama"), y luego cargar los filamentos en el extrusor. (tenga en cuenta que, independientemente del color de su impresión, debe cargar los 4 filamentos en las extrusoras y en el extremo caliente). A continuación, puede insertar la tarjeta SD en la máquina y elegir un archivo gcode de modelo 3D de prueba en la tarjeta SD. Para obtener más información, consulte los documentos a continuación.
- [:book: Documento en línea de la guía de operación](./2.Operation/Operation.md)
- [:blue_book: archivo PDF de la guía de operación](./2.Operation/Operation.pdf)
#### :page_with_curl: Más funciones
También puede leer los siguientes documentos para obtener una comprensión más profunda del extrusor (extremo caliente y cabezal de impresión) utilizado por su máquina, así como algunas funciones avanzadas de la máquina.
- [:book: Guía de uso de la función Mezclar colores][LINK_MIX_FEATURE]
- [:book: Introducción al hotend M4V6][LINK_M4V6]
- [:book: Imprimir desde PC](./2.Operation/PrintFromPC/readme.md)
- [:book: Guía de uso de funciones avanzadas](./2.Operation/Advance_Features.md)

## <a id="a3"> 3. Pruebe el archivo de código G </a>
**:pencil: ¿Qué es el código G en la impresión 3D?**
El código G es información o instrucciones que la impresora 3D requiere para imprimir un objeto tridimensional, es el lenguaje que la impresora 3D puede entender. Su software de corte genera G-Code, traduciendo un archivo de modelado 3D estándar como STL, objeto, archivo AMF, etc. :page_with_curl: [**Referencia 1**][GCODE_REF1] :page_with_curl: [**Referencia 2**][GCODE_REF2]     
Almacenamos algunos archivos gcode de prueba en la tarjeta SD, para ayudar a verificar si la máquina estaba funcionando correctamente o para demostrar qué funciones de impresión tiene esta máquina. Si no puede encontrar los archivos gcode de prueba en la tarjeta SD, descárguelos desde [:arrow_down: **aquí**](./3.TestGcode/Test_gcode.zip).
- **xyz_cube.gcode**: un archivo gcode de prueba simple utilizado para verificar si la máquina estaba funcionando bien.
- **dog.gcode**: un archivo de prueba de calidad de impresión clásico.
- **Vase.gcode**: Un jarrón de prueba.
   - **GradientMix_Vase.gcode**: un jarrón igual que vase.gcode pero con la función "mezcla de degradado" habilitada.
   - **RandomMix_Vase.gcode**: Un jarrón igual que vase.gcode pero habilitada la función de "mezcla aleatoria".
- **M4_4CTest.gcode**: un archivo de prueba base de 4 colores para impresora 3D con un extremo caliente M4.
- **M4_4C_BODY3D.gcode**: un archivo de prueba de 4 colores más grande.
- **16color_tower.gcode**: un archivo de prueba de color base 16 para mostrar el resultado de la mezcla de filamentos de diferentes colores.
- **level_test_310.gcode**: un archivo de prueba utilizado para verificar la planitud de la cama caliente (sin nivelación automática de la cama).
- **level_test_310-G29.gcode**: un archivo de prueba utilizado para verificar la planitud de la cama caliente (con nivelación automática de la cama).
**[:arrow_down: descargar más archivos gcode de prueba][M4_TEST_GCODE].**
 
## <a id="a4"> 4. Cortar </a>
**[:pencil: ¿Qué es el corte en impresión 3D?](https://en.wikipedia.org/wiki/Slicer_(3D_printing))**
Una cortadora es un software de generación de trayectorias de herramientas que se utiliza en la mayoría de los procesos de impresión 3D para la conversión de un modelo de objeto 3D en instrucciones específicas para la impresora. En particular, la conversión de un modelo en formato STL a comandos de impresora en formato de código g en la fabricación de filamentos fundidos y otros procesos similares.
- [:book:Documento en línea de la Guía del usuario de Slicer](./4.Slicing/readme.md)
- [:blue_book: Archivo PDF de la guía del usuario de Slicer](./4.Slicing/Slicing.pdf)

## <a id="a5"> 5. Firmware </a>
**:pencil: ¿Qué es el archivo bin del firmware y el código fuente?**
El archivo bin de firmware es la memoria exacta que se escribe en la memoria flash integrada.
El código fuente del firmware es la parte central del firmware. Nuestro código fuente de firmware se basa en [**marlin**](https://www.marlinfw.org).     
Puede descargar el archivo bin del firmware o el código fuente desde el siguiente enlace.
- [:arrow_down: archivo contenedor de firmware][LINK_FIRMWARE]
- [:arrow_down: código fuente del firmware][LINK_SOURCECODE]

## <a id="a6"> 6. Solución de problemas </a>
Si tiene algún problema al instalar y utilizar la impresora, primero intente encontrar una solución en el [:book: Documento en línea de solución de problemas][LINK_TROUBLESHOOTING]. Si no puede resolver este problema, contáctenos por correo electrónico (:email: support@zonestar3d.com).

## <a id="a7"> 7. Imprimir piezas </a>
Hay varios componentes de la máquina que están impresos y también hemos preparado algunas actualizaciones para usted. Si lo desea, puede descargarlos e imprimirlos y luego instalarlos en su máquina.

-----
## <a id="a8"> Funciones opcionales </a>
Hemos introducido algunas funciones opcionales para esta máquina; puede actualizar estas funciones en cualquier momento según sus preferencias. Si está interesado en esto, lea la guía de funciones de actualización opcionales para obtener información más detallada.
- [:book: Documento en línea de la guía de funciones de actualización opcional][Z9V5MK6_OPTION]
- [:blue_book: archivo pdf de la guía de funciones de actualización opcionales](./OptionalFeatures.pdf)

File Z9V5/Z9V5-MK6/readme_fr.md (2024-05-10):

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

----
## <a id="choose-language">:globe_with_meridians: Choose language </a>










----
# Guide de l'utilisateur pour l'imprimante 3D ZONESTAR Z9V5Pro-MK6

----
## :warning: ATTENTION S'IL VOUS PLAÎT
#### :loudspeaker: Avant d'utiliser la machine, veuillez lire attentivement [:book:"Précautions d'utilisation du M4V6"][M4V6_PRECAUTION].
#### :loudspeaker: Il faut charger 4 filaments simultanément sur le hotend M4V6, un fonctionnement incorrect peut bloquer le hotend de mélange de couleurs. Si le blocage de l'extrémité chaude est dû à un fonctionnement incorrect, il n'est pas couvert par la garantie. Pour savoir comment charger les filaments, veuillez vous référer à [:book: this guide][Z9V5MK6_LOADFILAMENT].
#### :loudspeaker: Si vous êtes débutant en imprimante 3D, veuillez lire attentivement le [Guide étape par étape][Z9V5MK6_STEPBYSTEP] et suivre les étapes à suivre.
- [:book: **Précautions d'utilisation de M4V6**][M4V6_PRECAUTION]
- [:book: **Comment charger correctement les filaments**][Z9V5MK6_LOADFILAMENT]
- [:book: **Guide étape par étape**][Z9V5MK6_STEPBYSTEP]
<!-- - [:blue_book: Fichier PDF du guide étape par étape](./step_by_step.pdf) -->

------
## :book: Contenu
- [**Guide d'installation**](#a1)
- [**Guide d'utilisation**](#a2)
- [**Tester les fichiers gcode**](#a3)
- [**Logiciel de découpage**](#a4)
- [**Micrologiciel**](#a5)
- [**Dépannage**](#a6)
- [**Imprimer les fichiers stl des pièces**](#a7)
- [**Fonctionnalités de mise à niveau facultatives**](#a8)

-----
## <a id="a1"> 1. Guide d'installation </a>
Tout d'abord, veuillez vous référer aux documents et vidéos suivants pour terminer l'installation et le câblage de la machine.
### Installation
- [:book: Document en ligne du guide d'installation](./1.Installation/Installation.md)
- [:blue_book: fichier PDF du guide d'installation](./1.Installation/Installation.pdf)
- [:clapper: Tutoriel vidéo du guide d'installation](https://youtu.be/TGHUVzV1Pg4)
### Câblage
- [:book: Document en ligne du guide de câblage](./1.Installation/Wiring.md)
- [:blue_book: fichier PDF du guide de câblage](./1.Installation/Wiring.pdf)
- [:art: Schéma de câblage](./1.Installation/Z9V5Pro_Wiring_Diagram.jpg)
- [:clapper: Tutoriel vidéo sur le câblage](https://youtu.be/tQQNLDOpdQU)

## <a id="a2"> 2. Guide d'utilisation </a>
### **Présentation du panneau de commande LCD**
Après avoir terminé l'installation et le câblage, veuillez consulter le guide ci-dessous pour savoir comment utiliser le panneau de commande (écran LCD) et comprendre les fonctions du menu LCD en général.
- [:book: Document en ligne du menu LCD](./2.Operation/LCDMENU_Description.md)
- [:blue_book: Fichier PDF du menu LCD](./2.Operation/LCDMENU_Description.pdf)
#### **Imprimez vos premiers travaux**
Vous pouvez maintenant essayer d'imprimer vos œuvres "Bonjour mot", avant de commencer l'impression, vous devez d'abord faire une simple correction de la hauteur du lit chaud (cela s'appelle "nivellement du lit"), puis charger les filaments dans l'extrudeuse. (veuillez noter que quelle que soit la couleur de votre impression, vous devez charger les 4 filaments dans les extrudeuses et la hot end). Ensuite, vous pouvez insérer la carte SD dans la machine et choisir un fichier gcode de modèle 3D de test dans la carte SD. Pour plus de détails, veuillez vous référer aux documents ci-dessous.  
- [:book: Document en ligne du Guide d'utilisation](./2.Operation/Operation.md)
- [:blue_book: fichier PDF du guide d'utilisation](./2.Operation/Operation.pdf)
#### :page_with_curl: Plus de fonctionnalités
Vous pouvez également lire les documents suivants pour mieux comprendre l'extrudeuse (extrémité chaude et tête d'impression) utilisée par votre machine, ainsi que certaines fonctionnalités avancées de la machine.
- [:book: Guide d'utilisation de la fonctionnalité Mélanger les couleurs][LINK_MIX_FEATURE]
- [:book: Introduction au M4V6 Hotend][LINK_M4V6]
- [:book: Imprimer depuis un PC](./2.Operation/PrintFromPC/readme.md)
- [:book: Guide d'utilisation des fonctionnalités avancées](./2.Operation/Advance_Features.md)

## <a id="a3"> 3. Testez le fichier G-code </a>
**:crayon: Qu'est-ce que le G-code dans l'impression 3D ?**
Le G-code est une information ou des instructions dont l'imprimante 3D a besoin pour imprimer un objet en 3 dimensions, c'est le langage que l'imprimante 3D peut comprendre. Le G-Code est généré par votre logiciel de découpage, en traduisant un fichier de modélisation 3D standard tel qu'un STL, un objet, un fichier AMF, etc. :page_with_curl: [**Referencia 1**][GCODE_REF1] :page_with_curl: [**Referencia 2**][GCODE_REF2]    
Nous avons stocké des fichiers gcode de test sur la carte SD, pour aider à vérifier si la machine fonctionnait correctement ou pour démontrer les fonctions d'impression dont dispose cette machine. Si vous ne trouvez pas les fichiers gcode de test sur la carte SD, veuillez les télécharger depuis [:arrow_down: **ici**](./3.TestGcode/Test_gcode.zip).   
- **xyz_cube.gcode**: Un simple fichier gcode de test utilisé pour vérifier si la machine fonctionnait bien.
- **dog.gcode** : Un fichier de test de qualité d'impression classique.
- **Vase.gcode**: Un vase de test.
   - **GradientMix_Vase.gcode**: Un vase identique à vase.gcode mais activé la fonction "gradient mix".
   - **RandomMix_Vase.gcode**: Un vase identique à vase.gcode mais activé la fonction "mélange aléatoire".
- **M4_4CTest.gcode** : Un fichier de test de base 4 couleurs pour imprimante 3D avec une extrémité chaude M4.
- **M4_4C_BODY3D.gcode**: Un fichier de test 4 couleurs plus grand.
- **16color_tower.gcode**: Un fichier de test de couleurs de base 16 pour montrer le résultat du mélange de filaments de différentes couleurs.
- **level_test_310.gcode**: Un fichier de test utilisé pour vérifier la planéité du lit chaud (sans nivellement automatique du lit).
- **level_test_310-G29.gcode**: Un fichier de test utilisé pour vérifier la planéité du lit chaud (avec nivellement automatique du lit).
**[:arrow_down: Téléchargez plus de fichiers gcode de test][M4_TEST_GCODE].**
 
## <a id="a4"> 4. Découpage </a>
**[:pencil: Qu'est-ce que le découpage en tranches dans l'impression 3D ?](https://en.wikipedia.org/wiki/Slicer_(3D_printing))**   
Un slicer est un logiciel de génération de parcours d'outil utilisé dans la majorité des processus d'impression 3D pour la conversion d'un modèle d'objet 3D en instructions spécifiques pour l'imprimante. En particulier, la conversion d'un modèle au format STL en commandes d'imprimante au format g-code dans la fabrication de filaments fondus et d'autres processus similaires.   
- [:book: Document en ligne du Guide de l'utilisateur de Slicer](./4.Slicing/readme.md)
- [:blue_book: Fichier PDF du guide de l'utilisateur du Slicer](./4.Slicing/Slicing.pdf)

## <a id="a5"> 5. Micrologiciel </a>
**:pencil: Qu'est-ce que le fichier bin du micrologiciel et le code source ?**   
Le fichier bin du micrologiciel est la mémoire exacte écrite sur la mémoire flash intégrée.    
Le code source du micrologiciel constitue la partie essentielle du micrologiciel. Le code source de notre firmware est basé sur [**marlin**](https://www.marlinfw.org).   
Vous pouvez télécharger le fichier bin du micrologiciel ou le code source à partir du lien ci-dessous.   
- [:arrow_down: fichier bin du micrologiciel][LINK_FIRMWARE]
- [:arrow_down: Code source du micrologiciel][LINK_SOURCECODE]

## <a id="a6"> 6. Dépannage </a>
Si vous rencontrez des problèmes lors de l'installation et de l'utilisation de l'imprimante, essayez d'abord de trouver une solution dans le [:book: Dépannage du document en ligne][LINK_TROUBLESHOOTING] d'abord. Si vous ne parvenez pas à résoudre ce problème, veuillez nous contacter par email (:email: support@zonestar3d.com).

## <a id="a7"> 7. Imprimer les pièces </a>
Plusieurs composants de la machine sont imprimés et nous avons également préparé quelques mises à niveau pour vous. Si vous le souhaitez, vous pouvez les télécharger et les imprimer, puis les installer sur votre machine.

-----
## <a id="a8"> Fonctionnalités facultatives </a>
Nous avons introduit quelques fonctionnalités optionnelles pour cette machine, vous pouvez mettre à niveau ces fonctionnalités à tout moment selon vos préférences. Si cela vous intéresse, veuillez lire le guide des fonctionnalités de mise à niveau facultatives pour obtenir des informations plus détaillées.   
- [:book: Document en ligne du guide des fonctionnalités de mise à niveau facultatives][Z9V5MK6_OPTION]
- [:blue_book: fichier pdf du guide des fonctionnalités de mise à niveau facultatives](./OptionalFeatures.pdf)

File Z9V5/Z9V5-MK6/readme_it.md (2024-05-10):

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

----
## <a id="choose-language">:globe_with_meridians: Choose language </a>










----
# Guida per l'utente per la stampante 3D ZONESTAR Z9V5Pro-MK6

----
## :warning: ATTENZIONE PER FAVORE
#### :loudspeaker: Prima di utilizzare la macchina, leggere attentamente [:book:"Precauzioni per l'utilizzo di M4V6"][M4V6_PRECAUTION].
#### :loudspeaker: È necessario caricare 4 filamenti sull'hotend M4V6 contemporaneamente, un funzionamento errato potrebbe bloccare l'hotend del colore misto. Se il blocco dell'hotend è causato da un funzionamento errato, non è coperto dalla garanzia. Per come caricare i filamenti, fare riferimento a [:book: questa guida][Z9V5MK6_LOADFILAMENT].
#### :loudspeaker: Se sei un principiante della stampante 3D, leggi attentamente il [:book: Guida passo passo][Z9V5MK6_STEPBYSTEP] e segui i passaggi da eseguire.
- [:book: **Precauzioni per l'utilizzo di M4V6**][M4V6_PRECAUTION]
- [:book: **Come caricare correttamente i filamenti**][Z9V5MK6_LOADFILAMENT]
- [:book: **Guida passo passo**][Z9V5MK6_STEPBYSTEP]
<!-- - [:blue_book: file PDF della guida passo passo](./step_by_step.pdf) -->

------
## :book: Contenuto
- [**Guida all'installazione**](#a1)
- [**Guida operativa**](#a2)
- [**Prova file gcode**](#a3)
- [**Software di slicing**](#a4)
- [**Firmware**](#a5)
- [**Risoluzione dei problemi**](#a6)
- [**Stampa file stl delle parti**](#a7)
- [**Funzioni di aggiornamento opzionali**](#a8)

-----
## <a id="a1"> 1. Guida all'installazione </a>
Innanzitutto, fare riferimento ai seguenti documenti e video per completare l'installazione e il cablaggio della macchina.
### Installazione
- [:book: Documento online della Guida all'installazione](./1.Installation/Installation.md)
- [:blue_book: file PDF della guida all'installazione](./1.Installation/Installation.pdf)
- [:clapper: Guida all'installazione Video tutorial](https://youtu.be/TGHUVzV1Pg4)
### Cablaggio
- [:book: Documento online della guida al cablaggio](./1.Installation/Wiring.md)
- [:blue_book: file PDF della guida al cablaggio](./1.Installazione/Wiring.pdf)
- [:art: Schema elettrico](./1.Installation/Z9V5Pro_Wiring_Diagram.jpg)
- [:clapper: Video tutorial sul cablaggio](https://youtu.be/tQQNLDOpdQU)

## <a id="a2"> 2. Guida operativa </a>
### **Introduzione al pannello di controllo LCD**
Dopo aver completato l'installazione e il cablaggio, dare un'occhiata alla guida seguente per sapere come utilizzare il pannello di controllo (schermo LCD) e comprendere le funzioni del menu LCD in generale.  
- [:book: Documento online del menu LCD](./2.Operation/LCDMENU_Description.md)
- [:blue_book: file PDF del menu LCD](./2.Operation/LCDMENU_Description.pdf)
#### **Stampa i tuoi primi lavori**
Adesso puoi provare a stampare i tuoi lavori "Hello word", prima di iniziare la stampa, devi prima fare una semplice correzione all'altezza del letto caldo (si chiama "bed leveling"), e poi caricare i filamenti nell'estrusore (tieni presente che, indipendentemente dal colore della stampa, è necessario caricare tutti e 4 i filamenti negli estrusori e nell'hot end). Successivamente, puoi inserire la scheda SD nella macchina e scegliere un file gcode del modello 3D di prova nella scheda SD. Per i dettagli fare riferimento ai documenti sottostanti.
- [:book: Documento online della Guida operativa](./2.Operation/Operation.md)
- [:blue_book: file PDF della Guida operativa](./2.Operazione/Operazione.pdf)
#### :page_with_curl: Altre funzionalità
È inoltre possibile leggere i seguenti documenti per acquisire una comprensione più approfondita dell'estrusore (estremità calda e testina di stampa) utilizzato dalla macchina, nonché di alcune funzionalità avanzate della macchina.
- [:book: Guida all'uso della funzione Mix Color][LINK_MIX_FEATURE]
- [:book: Introduzione all'hotend M4V6][LINK_M4V6]
- [:book: Stampa da PC](./2.Operation/PrintFromPC/readme.md)
- [:book: Guida all'uso delle funzionalità Advance](./2.Operation/Advance_Features.md)

## <a id="a3"> 3. Testare il file del codice G </a>
**:matita: cos'è il codice G nella stampa 3D?**
Il codice G è un'informazione o un'istruzione richiesta dalla stampante 3D per stampare un oggetto tridimensionale, è il linguaggio che la stampante 3D può comprendere. Il G-Code viene generato dal tuo software di slicing, traducendo un file di modellazione 3D standard come STL, oggetto, file AMF ecc.. :page_with_curl: [**Referencia 1**][GCODE_REF1] :page_with_curl: [**Referencia 2**][GCODE_REF2]     
Abbiamo memorizzato alcuni file gcode di prova nella scheda SD, per verificare se la macchina funzionava correttamente o per dimostrare quali funzioni di stampa ha questa macchina. Se non riesci a trovare i file gcode di prova nella scheda SD, scaricali da [:arrow_down: **qui**](./3.TestGcode/Test_gcode.zip).    
- **xyz_cube.gcode**: un semplice file gcode di prova utilizzato per verificare se la macchina funzionava bene.
- **dog.gcode**: un classico file di test della qualità di stampa.
- **Vase.gcode**: un vaso di prova.
   - **GradientMix_Vase.gcode**: un vaso uguale a vase.gcode ma abilitata la funzione "gradient mix".
   - **RandomMix_Vase.gcode**: un vaso uguale a vase.gcode ma abilitata la funzione "mix casuale".
- **M4_4CTest.gcode**: un file di test dei colori base 4 per stampante 3D con hot end M4.
- **M4_4C_BODY3D.gcode**: un file di prova a 4 colori più grande.
- **16color_tower.gcode**: un file di test del colore base 16 per mostrare il risultato di filamenti di colore diverso mescolati.
- **level_test_310.gcode**: un file di test utilizzato per verificare la planarità del letto caldo (senza livellamento automatico del letto).
- **level_test_310-G29.gcode**: un file di test utilizzato per verificare la planarità del letto caldo (con livellamento automatico del letto).
**[:arrow_down: Scarica altri file gcode di prova][M4_TEST_GCODE].**
 
## <a id="a4"> 4. Affettare </a>
**[:matita: cos'è l'affettamento nella stampa 3D?](https://en.wikipedia.org/wiki/Slicer_(3D_printing))**
Uno slicer è un software di generazione del percorso utensile utilizzato nella maggior parte dei processi di stampa 3D per la conversione di un modello di oggetto 3D in istruzioni specifiche per la stampante. In particolare, la conversione da un modello in formato STL a comandi di stampante in formato g-code nella fabbricazione di filamenti fusi e altri processi simili.    
- [:book:Documento online della Guida per l'utente di Slicer](./4.Slicing/readme.md)
- [:blue_book: File PDF della guida per l'utente di Slicer](./4.Slicing/Slicing.pdf)

## <a id="a5"> 5. Firmware </a>
**:matita: Cos'è il file bin del firmware e il codice sorgente?**
Il file bin del firmware è la memoria esatta che viene scritta nella flash incorporata.
Il codice sorgente del firmware è la parte principale del firmware. Il nostro codice sorgente del firmware è basato su [**marlin**](https://www.marlinfw.org).    
È possibile scaricare il file bin del firmware o il codice sorgente dal collegamento sottostante.   
- [:arrow_down: file bin del firmware][LINK_FIRMWARE]
- [:arrow_down: codice sorgente del firmware][LINK_SOURCECODE]

## <a id="a6"> 6. Risoluzione dei problemi </a>
In caso di problemi durante l'installazione e l'utilizzo della stampante, provare prima a trovare una soluzione nel [:book: Documento online sulla risoluzione dei problemi][LINK_TROUBLESHOOTING]. Se non riesci a risolvere questo problema, contattaci via email (:email: support@zonestar3d.com).

## <a id="a7"> 7. Stampa parti </a>
Sulla macchina sono presenti diversi componenti che vengono stampati e abbiamo anche preparato alcuni aggiornamenti per te. Se vuoi, puoi scaricarli, stamparli e poi installarli sul tuo computer.

-----
## <a id="a8"> Funzionalità opzionali </a>
Abbiamo introdotto alcune funzionalità opzionali per questa macchina, puoi aggiornare queste funzionalità in qualsiasi momento in base alle tue preferenze. Se sei interessato a questo, leggi la guida alle funzionalità di aggiornamento opzionali per ottenere informazioni più dettagliate.
- [:book: documento online della guida alle funzionalità di aggiornamento opzionali][Z9V5MK6_OPTION]
- [:blue_book: file pdf della guida alle funzionalità di aggiornamento opzionali](./OptionalFeatures.pdf)

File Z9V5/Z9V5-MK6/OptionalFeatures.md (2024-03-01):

#### [Download PDF file of this page](./OptionalFeatures.pdf)

-----
## Optional upgrade features
We have introduced some scalable features for this machine, and you can upgrade these features at any time according to your preferences.

### :new: Linear rail upgrade kit
Upgraded this item, the printing quality and stability will be improved, and it will help improve the flatness of the hot bed.
- **:book: [User guide](https://bit.ly/3qg5ht9)**  
- **:gift: [Buy in offical online store](https://bit.ly/43qQNVC) / [Buy in Aliexpress](https://www.aliexpress.us/item/1005005599988527.html)**

### :new: Large printing size upgrade kit
Upgraded this item, the maximus build volume can be extended to 500mmx500mmx400mm.   
- **:book: [User guide](https://github.com/ZONESTAR3D/Upgrade-kit-guide/tree/main/Z9V5_500x500)**  
- **:gift: [Buy in offical online store](http://bit.ly/3ZMDJI0) / [Buy in Aliexpress](https://www.aliexpress.us/item/3256805439021576.html)**

### :+1: WiFi module
Upgraded this item, you can remote control the 3d printer through PC or Mobile Phone.    
- **:book: [User guide](https://github.com/ZONESTAR3D/Upgrade-kit-guide/tree/main/WiFi)**    
- **:gift: [Buy in offical online store](https://bit.ly/3rB7mx1) / [Buy in Aliexpress](https://bit.ly/3i7aX4o)**   

### :+1: PEI Spring Steel Sheet Hotbed Sticker
PEI Spring Steel Sheet Hotbed Sticker is more durable than the original hot bed sticker. With the single side smooth hot bed facing up, it can also make the bottom of the print more smooth.
- **:gift: [Buy in offical online store](http://bit.ly/3GbI9Sr) / [Buy in Aliexpress](https://bit.ly/3VkmXOi)**  

### :+1: 4-IN-1-OUT Non-Mix color hotend
The E4 hot end does not require all four filaments to be loaded simultaneously during printing, and its color prime tower size can also be set smaller than M4 hot end when printing multi color. About what's different between M4 hotend and E4 hotend, please refer to [**here**](https://github.com/ZONESTAR3D/Upgrade-kit-guide/tree/main/HOTEND#4-extruders-hotend).     
- **:book: [User guide](https://github.com/ZONESTAR3D/Upgrade-kit-guide/tree/main/HOTEND/E4)**
- **:gift: [Buy in offical online store](https://bit.ly/39qDtKp) / [Buy in Aliexpress](https://www.aliexpress.com/item/3256802765462947.html)**  

### :+1: Direct drive extruder
Upgraded this item, you can print flexible filaments (such as TPU). 
- **:book: [User guide](https://github.com/ZONESTAR3D/Upgrade-kit-guide/tree/main/Direct%20Drive%20Extrruder)**
- **:gift: [Buy in offical online store](https://bit.ly/3CA0QvV) / [Buy in Aliexpress](https://bit.ly/3TZxkGp)**   

### :fire: Laser engine
Upgraded this item, you can turn the 3D printer into a simple laser engraving machine. 
- **:book: [User guide](https://github.com/ZONESTAR3D/Upgrade-kit-guide/tree/main/Laser%20Engraving)** 
- **:gift: [Buy in offical online store](http://bit.ly/3IbekCr) / [Buy in Aliexpress](http://bit.ly/3G3cJw1)**  

### :cool: Automatic Repeat Printing Module
Upgraded this item, the Z9V5 can realize continuous automatic printing 3d prints. 
- **:book: [User guide](https://github.com/ZONESTAR3D/Upgrade-kit-guide/tree/main/Auto_Repeat_Printing)**   
- **:gift: [Buy at offical online store](http://bit.ly/3Gsi5SS) / [Buy in Aliexpress](http://bit.ly/3Iff8Xg)**

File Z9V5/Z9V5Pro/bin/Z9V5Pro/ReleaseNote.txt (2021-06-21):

2021-1-18  Z9V5Pro_V1_0_0.bin 	First issue
           Z9V5_V1_0_0_EN.bin 	First issue

2021-1-26  Z9V5Pro_V1_0_1.bin.
           Z9V5_V1_0_1_EN.bin. 
1.Dwin screen refreshes the display after receiving m166 m167 instruction;
2.Automatic retraction speed modification;
3.fixed some other known bugs;

2021-2-4   Z9V5Pro_V1_0_3.bin.
1.Add the function of all extruders moving at the same time in the move menu;
2.fixed some other known bugs;

2021-2-25   Z9V5Pro_V1_0_4
1.Modify the bug of manual extrusion of extruder in the move menu;
2.Modify the display of several menu names;

2021-3-9   Z9V5Pro_V1_0_5
1.Modifying bed leveling display；
2.Fix several known bugs

2021-3-18   Z9V5Pro_V1_0_6
1.Add WIFI function；

2021-4-18   Z9V5Pro_V1_0_7
[CHG] Improve the auto leveling feature for glass bed
Following the below steps to do:
1. Adjust the Z axis adjust screws (left and right) to the bottom as far as possible
2. Do Level corners(Menu>>Prepare>>Bed Levling), let the 4 corners on the same heigth as far as possible
3. copy level_test_310.gcode file to SD card and print it, if the bed is enough leveling, do need to enable bed auto leveling feature.
4. Turn on the auto leveling feature(MENU>>Config>>configure>>Auto Leveling: ON)
5. Remove the glass
6. do Menu>>Prepare>>Bed Levling>>Catch Z-offset
7. do Menu>>Prepare>>Bed Levling>>AutoLevling
8. Print "level_test_310.gcode" file again to check.

PS: if you find the nozzle is too Heigth/Low when printing the first layer, Redunce/Add the coating thickness value on menu (Config>>configure>>Coating Thickness)

2021-5-15   Z9V5Pro_V1_0_8_beta
[CHG]1. Save WiFi On Off
[CHG]2. Remove unactived menu option of config when printing from SD card

2021-6-19   Z9V5Pro_V1_1_0
[CHG]1. Optimize the menu arrangement and display effect.

[CHG]2. Fix the confirmation logic of WiFi module.

[CHG]
3. Optimize automatic leveling function:

3.1. Add probe offset setting (usually, if the catch offset effect is not good and the height of the nozzle is not suitable when printing the first layer after auto leveling, you need to adjust babystepz. You can add babystep value to probezofaffset and do auto leveling again)

3.2 Add Probing heigh table display for automatic leveling.

For more description of the auto leveling function, please refer to the directory "bed auto leveling"
[CHG]4. Change the text of the menu item "bed coasting" to "home Z offset"

[BUG]5. Fixed several known bugs

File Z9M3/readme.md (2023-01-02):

### :globe_with_meridians: Choose Language (Translated by google)
(https://github-com.translate.goog/ZONESTAR3D/Z9/tree/main/Z9M3?_x_tr_sl=en&_x_tr_tl=es)
(https://github-com.translate.goog/ZONESTAR3D/Z9/tree/main/Z9M3?_x_tr_sl=en&_x_tr_tl=fr)
(https://github-com.translate.goog/ZONESTAR3D/Z9/tree/main/Z9M3?_x_tr_sl=en&_x_tr_tl=pt)
(https://github-com.translate.goog/ZONESTAR3D/Z9/tree/main/Z9M3?_x_tr_sl=en&_x_tr_tl=de)
(https://github-com.translate.goog/ZONESTAR3D/Z9/tree/main/Z9M3?_x_tr_sl=en&_x_tr_tl=it)
(https://github-com.translate.goog/ZONESTAR3D/Z9/tree/main/Z9M3?_x_tr_sl=en&_x_tr_tl=pl)
(https://github-com.translate.goog/ZONESTAR3D/Z9/tree/main/Z9M3?_x_tr_sl=en&_x_tr_tl=ru)
(https://github-com.translate.goog/ZONESTAR3D/Z9/tree/main/Z9M3?_x_tr_sl=en&_x_tr_tl=pt)
(https://github-com.translate.goog/ZONESTAR3D/Z9/tree/main/Z9M3?_x_tr_sl=en&_x_tr_tl=el)

(https://github-com.translate.goog/ZONESTAR3D/Z9/tree/main/Z9M3?_x_tr_sl=en&_x_tr_tl=ja)
(https://github-com.translate.goog/ZONESTAR3D/Z9/tree/main/Z9M3?_x_tr_sl=en&_x_tr_tl=ko)
(https://github-com.translate.goog/ZONESTAR3D/Z9/tree/main/Z9M3?_x_tr_sl=en&_x_tr_tl=id)
(https://github-com.translate.goog/ZONESTAR3D/Z9/tree/main/Z9M3?_x_tr_sl=en&_x_tr_tl=th)
(https://github-com.translate.goog/ZONESTAR3D/Z9/tree/main/Z9M3?_x_tr_sl=en&_x_tr_tl=vi)
(https://github-com.translate.goog/ZONESTAR3D/Z9/tree/main/Z9M3?_x_tr_sl=en&_x_tr_tl=iw)
(https://github-com.translate.goog/ZONESTAR3D/Z9/tree/main/Z9M3?_x_tr_sl=en&_x_tr_tl=ar)
(https://github-com.translate.goog/ZONESTAR3D/Z9/tree/main/Z9M3?_x_tr_sl=en&_x_tr_tl=tr)
(https://github-com.translate.goog/ZONESTAR3D/Z9/tree/main/Z9M3?_x_tr_sl=en&_x_tr_tl=zh-CN)

-----
### [:file_folder: The 3rd Z9M3 Documents](./Z9T/)
[:arrow_down: **Download the 3rd Z9M3 Documents in one go**](https://downgit.github.io/#/home?url=https:%2F%2Fgithub.com%2FZONESTAR3D%2FZ9%2Ftree%2Fmain%2FZ9M3%2FZ9T)  
### [:file_folder: The 4th Z9M3 Documents](./Z9F/)
[:arrow_down: **Download the 4th Z9M3 Documents in one go**](https://downgit.github.io/#/home?url=https:%2F%2Fgithub.com%2FZONESTAR3D%2FZ9%2Ftree%2Fmain%2FZ9M3%2FZ9F)

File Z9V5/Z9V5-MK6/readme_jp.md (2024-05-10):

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

----
## <a id="choose-language">:globe_with_meridians: Choose language </a>










----
# ZONESTAR Z9V5Pro-MK6 3D プリンター ユーザーガイド

----
## :warning: 注意してください
#### :loudspeaker: 本機をご使用になる前に、[:book:「M4V6 ご使用上の注意」][M4V6_PRECAUTION]をよくお読みください。
#### :loudspeaker: M4V6 ホットエンドに 4 つのフィラメントを同時にロードする必要があります。誤った操作を行うと、ミックス カラー ホットエンドがブロックされる可能性があります。 誤操作によるホットエンドの詰まりは保証の対象外となります。 フィラメントのロード方法については、[:book:本書][Z9V5MK6_LOADFILAMENT]を参照してください。
#### :loudspeaker: 3D プリンターの初心者の方は、[:book: ステップバイステップ ガイド][Z9V5MK6_STEPBYSTEP] をよく読み、手順に従ってください。
- [:book: **M4V6 使用上の注意事項**][M4V6_PRECAUTION]
- [:book: **フィラメントを正しくロードする方法**][Z9V5MK6_LOADFILAMENT]
- [:book: **ステップバイステップガイド**][Z9V5MK6_STEPBYSTEP]

------
## :book: 目次
- [**インストールガイド**](#a1)
- [**操作ガイド**](#a2)
- [**gcode ファイルをテスト**](#a3)
- [**スライスソフトウェア**](#a4)
- [**ファームウェア**](#a5)
- [**トラブルシューティング**](#a6)
- [**パーツ stl ファイルを印刷**](#a7)
- [**オプションのアップグレード機能**](#a8)

-----
## <a id="a1"> 1. インストール ガイド </a>
まず、以下の資料とビデオを参照して、機械の設置と配線を完了してください。
### インストール
- [:book: インストール ガイド オンライン ドキュメント](./1.installation/installation.md)
- [:blue_book: インストール ガイド PDF ファイル](./1.インストール/インストール.pdf)
- [:clapper: インストールガイドビデオチュートリアル](https://youtu.be/TGHUVzV1Pg4)
### 配線
- [:book: 配線ガイド オンライン ドキュメント](./1. Installation/Wiring.md)
- [:blue_book: 配線ガイド PDF ファイル](./1.取り付け/配線.pdf)
- [:art: 配線図](./1.installation/Z9V5Pro_Wiring_Diagram.jpg)
- [:clapper: 配線ビデオチュートリアル](https://youtu.be/tQQNLDOpdQU)

## <a id="a2"> 2. 操作ガイド </a>
### **LCD コントロール パネルの概要**
設置と配線が完了したら、以下のガイドを参照してコントロールパネル (LCD 画面) の使用方法を知り、LCD メニューの機能を全体的に理解してください。
- [:book: LCD メニュー オンライン ドキュメント](./2.Operation/LCDMENU_Description.md)
- [:blue_book: LCD メニュー PDF ファイル](./2.Operation/LCDMENU_Description.pdf)
#### **最初の作品を印刷します**
これで、「Hello word」作品を印刷してみることができます。印刷を開始する前に、まずホット ベッドの高さを簡単に修正し (「ベッド レベリング」と呼ばれます)、次にフィラメントを押出機にロードする必要があります。 (プリントの色に関係なく、4 本のフィラメントすべてを押出機とホットエンドにロードする必要があることに注意してください)。 次に、SD カードをマシンに挿入し、SD カード内のテスト用 3D モデル gcode ファイルを選択できます。 詳細は以下の資料をご参照ください。
- [:book: 操作ガイド オンラインドキュメント](./2.Operation/Operation.md)
- [:blue_book: 操作ガイド PDF ファイル](./2.Operation/Operation.pdf)
#### :page_with_curl: その他の機能
また、次のドキュメントを読んで、マシンで使用される押出機 (ホットエンドおよびプリントヘッド) やマシンの高度な機能についてより深く理解することもできます。
- [:book: ミックスカラー機能使用ガイド][LINK_MIX_FEATURE]
- [:book: M4V6 Hotend の紹介][LINK_M4V6]
- [:book: PC から印刷](./2.Operation/PrintFromPC/readme.md)
- [:book: Advanced 機能使用ガイド](./2.Operation/Advance_Feature.md)

## <a id="a3"> 3. G コード ファイルをテストします </a>
**:pencil: 3D プリントにおける G コードとは何ですか?**
G コードとは、3D プリンターが 3 次元オブジェクトを印刷するために必要な情報、または命令であり、3D プリンターが理解できる言語です。 G コードは、STL、オブジェクト、AMF ファイルなどの標準 3D モデリング ファイルを変換することにより、スライシング ソフトウェアによって生成されます。 :page_with_curl: [**参照 1**][GCODE_REF1] :page_with_curl: [**参照 2**][GCODE_REF2]   
マシンが適切に動作しているかどうかを確認したり、このマシンにどのような印刷機能があるかを実証したりするために、いくつかのテスト gcode ファイルを SD カードに保存しました。 SD カード内にテスト gcode ファイルが見つからない場合は、[:arrow_down: **ここ**](./3.TestGcode/Test_gcode.zip) からダウンロードしてください。  
- **xyz_cube.gcode**: マシンが正常に動作しているかどうかを確認するために使用される単純なテスト gcode ファイル。  
- **dog.gcode**: 古典的な印刷品質テスト ファイル。
- **Vase.gcode**: テスト用の花瓶。
   - **GradientMix_Vase.gcode**: vase.gcode と同じ花瓶ですが、「グラデーション ミックス」機能が有効になっています。
   - **RandomMix_Vase.gcode**: vase.gcode と同じ花瓶ですが、「ランダム ミックス」機能が有効になっています。
- **M4_4CTest.gcode**: M4 ホット エンドを備えた 3D プリンター用の基本 4 色のテスト ファイル。
- **M4_4C_BODY3D.gcode**: より大きな 4 色のテスト ファイル。
- **16color_tower.gcode**: 異なる色のフィラメントを混合した結果を示す基本 16 色のテスト ファイル。
- **level_test_310.gcode**: ホット ベッドの平坦度を検証するために使用されるテスト ファイル (ベッドの自動レベリングなし)。
- **level_test_310-G29.gcode**: ホット ベッドの平坦度 (ベッドの自動レベリング付き) を検証するために使用されるテスト ファイル。
**[:arrow_down: さらにテスト gcode ファイルをダウンロード][M4_TEST_GCODE].**
 
## <a id="a4"> 4. スライス </a>
**[:pencil: 3D プリントにおけるスライスとは何ですか?](https://en.wikipedia.org/wiki/Slicer_(3D_printing))**
スライサーは、3D オブジェクト モデルをプリンターの特定の命令に変換するために、ほとんどの 3D プリンティング プロセスで使用されるツールパス生成ソフトウェアです。 特に、溶融フィラメント製造やその他の同様のプロセスにおける STL 形式のモデルから G コード形式のプリンタ コマンドへの変換。   
- [:book:スライサー ユーザー ガイド オンライン ドキュメント](./4.Slicing/readme.md)
- [:blue_book: スライサー ユーザーガイド PDF ファイル](./4.Slicing/Slicing.pdf)

## <a id="a5"> 5. ファームウェア </a>
**:pencil: ファームウェアの bin ファイルとソース コードとは何ですか?**
ファームウェア bin ファイルは、内蔵フラッシュに書き込まれる正確なメモリです。   
ファームウェアのソース コードは、ファームウェアの中核部分です。 当社のファームウェアのソース コードは [**marlin**](https://www.marlinfw.org) に基づいています。   
以下のリンクからファームウェアの bin ファイルまたはソース コードをダウンロードできます。  
- [:arrow_down: ファームウェア bin ファイル][LINK_FIRMWARE]
- [:arrow_down: ファームウェアのソース コード][LINK_SOURCECODE]

## <a id="a6"> 6. トラブルシューティング </a>
プリンタのインストールと使用に問題がある場合は、まず [:book: トラブルシューティング オンライン ドキュメント][LINK_TROUBLESHOOTING] から解決策を見つけてみてください。 この問題を解決できない場合は、電子メール (:email: support@zonestar3d.com) でお問い合わせください。

## <a id="a7"> 7. パーツの印刷 </a>
マシンには印刷されるいくつかのコンポーネントがあり、いくつかのアップグレードも用意されています。 必要に応じて、ダウンロードして印刷し、マシンにインストールできます。

-----
## <a id="a8"> オプション機能 </a>
このマシンにはいくつかのオプション機能が導入されており、好みに応じていつでもこれらの機能をアップグレードできます。 これに興味がある場合は、「オプションのアップグレード機能ガイド」を読んで、より詳細な情報を入手してください。
- [:book: オプションのアップグレード機能ガイドのオンライン ドキュメント][Z9V5MK6_OPTION]
- [:blue_book: オプションのアップグレード機能ガイド PDF ファイル](./OptionalFeature.pdf)

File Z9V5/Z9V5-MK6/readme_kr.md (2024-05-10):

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

----
## <a id="choose-language">:globe_with_meridians: Choose language </a>










----
# ZONESTAR Z9V5Pro-MK6 3D 프린터 사용 설명서

----
## :warning: 주의하세요
#### :loudspeaker: 기기를 사용하기 전에 [:book:"M4V6 사용 시 주의사항"][M4V6_PRECAUTION]을 주의 깊게 읽어보세요.
#### :loudspeaker: M4V6 핫엔드에 4개의 필라멘트를 동시에 로드해야 합니다. 잘못된 작동으로 인해 혼합 색상 핫엔드가 차단될 수 있습니다. 잘못된 작동으로 인해 핫엔드가 막힌 경우에는 보증이 적용되지 않습니다. 필라멘트 로딩 방법은 [:book: 이 가이드][Z9V5MK6_LOADFILAMENT]를 참조하세요.
#### :loudspeaker: 3D 프린터 초보자라면 [:book: 단계별 가이드][Z9V5MK6_STEPBYSTEP]를 주의 깊게 읽고 단계를 따르세요.
- [:book: **M4V6 사용 시 주의사항**][M4V6_PRECAUTION]
- [:book: **필라멘트를 올바르게 로드하는 방법**][Z9V5MK6_LOADFILAMENT]
- [:book: **단계별 가이드**][Z9V5MK6_STEPBYSTEP]

------
## :book: 목차
- [**설치 가이드**](#a1)
- [**조작안내**](#a2)
- [**gcode 파일 테스트**](#a3)
- [**슬라이싱 소프트웨어**](#a4)
- [**펌웨어**](#a5)
- [**문제 해결**](#a6)
- [**부품 stl 파일 인쇄**](#a7)
- [**선택적 업그레이드 기능**](#a8)

-----
## <a id="a1"> 1. 설치 가이드 </a>
먼저, 기계의 설치 및 배선을 완료하기 위해 다음 문서와 비디오를 참조하십시오.
### 설치
- [:book: 설치 가이드 온라인 문서](./1.Installation/Installation.md)
- [:blue_book: 설치 가이드 PDF 파일](./1.Installation/Installation.pdf)
- [:clapper: 설치 가이드 동영상 튜토리얼](https://youtu.be/TGHUVzV1Pg4)
### 배선
- [:book: 배선 가이드 온라인 문서](./1.Installation/Wiring.md)
- [:blue_book: 배선 가이드 PDF 파일](./1.Installation/Wiring.pdf)
- [:art: 배선도](./1.Installation/Z9V5Pro_Wiring_Diagram.jpg)
- [:clapper: 배선 동영상 튜토리얼](https://youtu.be/tQQNLDOpdQU)

## <a id="a2"> 2. 운영 안내 </a>
### **LCD 제어판 소개**
설치 및 결선 작업이 완료되면 아래의 가이드를 통해 제어판(LCD 화면)의 사용법을 숙지하시고, LCD 메뉴의 전반적인 기능을 이해하시기 바랍니다.
- [:book: LCD 메뉴 온라인 문서](./2.Operation/LCDMENU_Description.md)
- [:blue_book: LCD 메뉴 PDF 파일](./2.Operation/LCDMENU_Description.pdf)
#### **첫 번째 작품을 인쇄하세요**
이제 "Hello word" 작품을 인쇄해 볼 수 있습니다. 인쇄를 시작하기 전에 먼저 핫 베드의 높이를 간단히 수정한 다음("베드 레벨링"이라고 함) 필라멘트를 압출기에 로드해야 합니다. (인쇄물의 색상에 관계없이 4개의 필라멘트를 모두 압출기와 핫엔드에 로드해야 합니다.) 다음으로 SD 카드를 기기에 삽입하고 SD 카드에서 테스트용 3D 모델 gcode 파일을 선택할 수 있습니다. 자세한 사항은 아래 문서를 참고하시기 바랍니다.
- [:book: 운영 가이드 온라인 문서](./2.Operation/Operation.md)
- [:blue_book: 조작 가이드 PDF 파일](./2.Operation/Operation.pdf)
#### :page_with_curl: 추가 기능
또한 다음 문서를 읽고 기계에서 사용되는 압출기(핫 엔드 및 프린트 헤드)와 기계의 일부 고급 기능에 대해 더 깊이 이해할 수 있습니다.
- [:book: 믹스 컬러 기능 이용 안내][LINK_MIX_FEATURE]
- [:book: M4V6 핫엔드 소개][LINK_M4V6]
- [:book: PC에서 인쇄](./2.Operation/PrintFromPC/readme.md)
- [:book: 고급 기능 사용 가이드](./2.Operation/Advance_Features.md)

## <a id="a3"> 3. G 코드 파일 테스트 </a>
**:연필: 3D 프린팅에서 G 코드란 무엇입니까?**
G-code는 3D 프린터가 3차원 물체를 출력하기 위해 필요한 정보 또는 명령어로, 3D 프린터가 이해할 수 있는 언어입니다. G-코드는 STL, 객체, AMF 파일 등과 같은 표준 3D 모델링 파일을 변환하여 슬라이싱 소프트웨어에 의해 생성됩니다. :page_with_curl: [**참조 1**][GCODE_REF1] :page_with_curl: [**참조 2**][GCODE_REF2]
기계가 제대로 작동하는지 확인하거나 이 기계에 어떤 인쇄 기능이 있는지 보여주기 위해 일부 테스트 gcode 파일을 SD 카드에 저장했습니다. SD 카드에서 테스트 gcode 파일을 찾을 수 없는 경우 [:arrow_down: **여기**](./3.TestGcode/Test_gcode.zip)에서 다운로드하세요.
- **xyz_cube.gcode**: 머신이 제대로 작동하는지 확인하는 데 사용되는 간단한 테스트 gcode 파일입니다.
- **dog.gcode**: 클래식 인쇄 품질 테스트 파일입니다.
- **Vase.gcode**: 테스트 꽃병입니다.
   - **GradientMix_Vase.gcode**: vase.gcode와 동일하지만 "그라디언트 믹스" 기능이 활성화된 꽃병입니다.
   - **RandomMix_Vase.gcode**: vase.gcode와 동일하지만 "랜덤 믹스" 기능이 활성화된 꽃병입니다.
- **M4_4CTest.gcode**: M4 핫엔드를 갖춘 3D 프린터용 기본 4색 테스트 파일입니다.
- **M4_4C_BODY3D.gcode**: 더 큰 4색 테스트 파일입니다.
- **16color_tower.gcode**: 서로 다른 색상의 필라멘트를 혼합한 결과를 보여주는 기본 16색 테스트 파일입니다.
- **level_test_310.gcode**: 핫베드 평탄도를 확인하는 데 사용되는 테스트 파일입니다(베드 자동 레벨링 없음).
- **level_test_310-G29.gcode**: 핫베드 평탄도(베드 자동 레벨링 포함)를 확인하는 데 사용되는 테스트 파일입니다.
**[:arrow_down: 추가 테스트 gcode 파일 다운로드][M4_TEST_GCODE].**
 
## <a id="a4"> 4. 자르기 </a>
**[:pencil: 3D 프린팅에서 슬라이싱이란 무엇입니까?](https://en.wikipedia.org/wiki/Slicer_(3D_printing))**
슬라이서는 3D 객체 모델을 프린터의 특정 지침으로 변환하기 위해 대부분의 3D 프린팅 프로세스에 사용되는 도구 경로 생성 소프트웨어입니다. 특히 융합 필라멘트 제조 및 기타 유사한 프로세스에서 STL 형식의 모델을 g-코드 형식의 프린터 명령으로 변환합니다.
- [:book:Slicer 사용자 가이드 온라인 문서](./4.Slicing/readme.md)
- [:blue_book: 슬라이서 사용 설명서 PDF 파일](./4.Slicing/Slicing.pdf)

## <a id="a5"> 5. 펌웨어 </a>
**:연필: 펌웨어 bin 파일과 소스 코드는 무엇입니까?**
펌웨어 bin 파일은 내장 플래시에 기록되는 정확한 메모리입니다.   
펌웨어 소스 코드는 펌웨어의 핵심 부분입니다. 당사의 펌웨어 소스 코드는 [**marlin**](https://www.marlinfw.org)을 기반으로 합니다.   
아래 링크에서 펌웨어 bin 파일이나 소스코드를 다운로드 받으실 수 있습니다.   
- [:arrow_down: 펌웨어 bin 파일][LINK_FIRMWARE]
- [:arrow_down: 펌웨어 소스 코드][LINK_SOURCECODE]

## <a id="a6"> 6. 문제 해결 </a>
프린터 설치 및 사용에 문제가 있는 경우 먼저 [:book: 문제 해결 온라인 문서][LINK_TROUBLESHOOTING]에서 해결 방법을 찾아보세요. 이 문제를 해결할 수 없는 경우 이메일(:email: support@zonestar3d.com)로 문의해 주세요.

## <a id="a7"> 7. 부품 인쇄 </a>
기계에는 인쇄된 여러 구성 요소가 있으며, 우리는 또한 귀하를 위해 몇 가지 업그레이드를 준비했습니다. 원하는 경우 다운로드하여 인쇄한 다음 컴퓨터에 설치할 수 있습니다.

-----
## <a id="a8"> 선택 기능 </a>
우리는 이 기기에 몇 가지 옵션 기능을 도입했습니다. 귀하는 귀하의 선호에 따라 언제든지 이러한 기능을 업그레이드할 수 있습니다. 이에 관심이 있으시면 선택적 업그레이드 기능 가이드를 읽어 자세한 정보를 얻으십시오.
- [:book: 선택적 업그레이드 기능 가이드 온라인 문서][Z9V5MK6_OPTION]
- [:blue_book: 선택적 업그레이드 기능 가이드 pdf 파일](./OptionalFeatures.pdf)

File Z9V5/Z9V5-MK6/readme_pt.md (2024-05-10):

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

  ----
  ## <a id="choose-language">:globe_with_meridians: Choose language </a>
  
  
  
  
  
  
  
  
  

----
# Guia do usuário para impressora 3D ZONESTAR Z9V5Pro-MK6

----
## :warning: ATENÇÃO POR FAVOR
#### :loudspeaker: Antes de usar a máquina, leia [:book:"Precauções para usar M4V6"][M4V6_PRECAUTION] com atenção.
#### :loudspeaker: Deve carregar 4 filamentos no hotend M4V6 simultaneamente, a operação incorreta pode bloquear o hotend de cores misturadas. Se o bloqueio do hot end for causado por operação incorreta, não será coberto pela garantia. Para saber como carregar filamentos, consulte [:book: this guide][Z9V5MK6_LOADFILAMENT].
#### :loudspeaker: Se você é iniciante em impressora 3D, leia atentamente o [Guia passo a passo] [Z9V5MK6_STEPBYSTEP] e siga as etapas a seguir.
- [:book: **Precauções para usar M4V6**][M4V6_PRECAUTION]
- [:book: **Como carregar filamentos corretamente**][Z9V5MK6_LOADFILAMENT]
- [:book: **Guia passo a passo**][Z9V5MK6_STEPBYSTEP]
<!-- - [:blue_book: arquivo PDF do guia passo a passo](./step_by_step.pdf) -->

------
## :book: Conteúdo
- [**Guia de instalação**](#a1)
- [**Guia de operação**](#a2)
- [**Teste arquivos gcode**](#a3)
- [**Software de fatiamento**](#a4)
- [**Firmware**](#a5)
- [**Soluções de problemas**](#a6)
- [**Imprimir arquivos stl de peças**](#a7)
- [**Recursos opcionais de atualização**](#a8)

-----
## <a id="a1"> 1. Guia de instalação </a>
Primeiro, consulte os seguintes documentos e vídeos para concluir a instalação e fiação da máquina.
### Instalação
- [:book: Documento on-line do guia de instalação](./1.Installation/Installation.md)
- [:blue_book: Arquivo PDF do guia de instalação](./1.Installation/Installation.pdf)
- [:clapper: Tutorial em vídeo do guia de instalação](https://youtu.be/TGHUVzV1Pg4)
### Fiação
- [:book: Documento on-line do guia de fiação](./1.Installation/Wiring.md)
- [:blue_book: Arquivo PDF do guia de fiação](./1.Installation/Wiring.pdf)
- [:art: Diagrama de fiação](./1.Installation/Z9V5Pro_Wiring_Diagram.jpg)
- [:clapper: Tutorial em vídeo de fiação](https://youtu.be/tQQNLDOpdQU)

## <a id="a2"> 2. Guia de operação </a>
### **Introdução ao painel de controle LCD**
Depois de concluir a instalação e a fiação, consulte o guia abaixo para saber como usar o painel de controle (tela LCD) e entender as funções do menu LCD em geral.
- [:book: Documento on-line do menu LCD](./2.Operation/LCDMENU_Description.md)
- [:blue_book: arquivo PDF do menu LCD](./2.Operation/LCDMENU_Description.pdf)
#### **Imprima seus primeiros trabalhos**
Agora você pode tentar imprimir seus trabalhos de "Hello word", antes de iniciar a impressão, primeiro você precisa fazer uma correção simples na altura da cama quente (é chamada de "nivelamento da cama"), e depois carregar os filamentos na extrusora (observe que independentemente da cor da sua impressão, você precisa carregar todos os 4 filamentos nas extrusoras e no hot end). Em seguida, você pode inserir o cartão SD na máquina e escolher um arquivo gcode do modelo 3D de teste no cartão SD. Para obter detalhes, consulte os documentos abaixo.
- [:book: Documento on-line do guia de operação](./2.Operation/Operation.md)
- [:blue_book: arquivo PDF do guia de operação](./2.Operation/Operation.pdf)
#### :page_with_curl: Mais recursos
Você também pode ler os documentos a seguir para obter uma compreensão mais profunda da extrusora (hot end e cabeçote de impressão) usada pela sua máquina, bem como alguns recursos avançados da máquina.
- [:book: Guia de uso do recurso Mix Color][LINK_MIX_FEATURE]
- [:book: introdução ao Hotend M4V6][LINK_M4V6]
- [:book: Imprimir do PC](./2.Operation/PrintFromPC/readme.md)
- [:book: Guia de uso de recursos avançados](./2.Operation/Advance_Features.md)

## <a id="a3"> 3. Teste o arquivo de código G </a>
**:lápis: O que é código G na impressão 3D?**
Código G são informações ou instruções que a impressora 3D requer para imprimir um objeto tridimensional, é a linguagem que a impressora 3D pode entender. O G-Code é gerado pelo seu software de fatiamento, traduzindo um arquivo de modelagem 3D padrão, como STL, objeto, arquivo AMF etc. **][GCODE_REF2]    
Armazenamos alguns arquivos gcode de teste no cartão SD, para ajudar a verificar se a máquina estava funcionando corretamente ou para demonstrar quais funções de impressão esta máquina possui. Se você não conseguir encontrar os arquivos gcode de teste no cartão SD, faça download em [:arrow_down: **aqui**](./3.TestGcode/Test_gcode.zip).    
- **xyz_cube.gcode**: Um arquivo gcode de teste simples usado para verificar se a máquina estava funcionando bem.
- **dog.gcode**: Um arquivo clássico de teste de qualidade de impressão.
- **Vase.gcode**: um vaso de teste.
   - **GradientMix_Vase.gcode**: Um vaso igual a vase.gcode, mas com o recurso "gradient mix" habilitado.
   - **RandomMix_Vase.gcode**: Um vaso igual a vase.gcode, mas com recurso de "mix aleatório" habilitado.
- **M4_4CTest.gcode**: Um arquivo de teste de base de 4 cores para impressora 3D com hot end M4.
- **M4_4C_BODY3D.gcode**: Um arquivo de teste maior com 4 cores.
- **16color_tower.gcode**: Um arquivo de teste de base de 16 cores para mostrar o resultado da mistura de filamentos de cores diferentes.
- **level_test_310.gcode**: Um arquivo de teste usado para verificar o nivelamento da cama quente (sem nivelamento automático da cama).
- **level_test_310-G29.gcode**: Um arquivo de teste usado para verificar o nivelamento da cama quente (com nivelamento automático da cama).
**[:arrow_down: Baixe mais arquivos gcode de teste][M4_TEST_GCODE].**
 
## <a id="a4"> 4. Fatiar </a>
**[:pencil: O que é fatiar na impressão 3D?](https://en.wikipedia.org/wiki/Slicer_(3D_printing))**
Um fatiador é um software de geração de percurso usado na maioria dos processos de impressão 3D para a conversão de um modelo de objeto 3D em instruções específicas para a impressora. Em particular, a conversão de um modelo em formato STL para comandos de impressora em formato de código G na fabricação de filamentos fundidos e outros processos semelhantes.   
- [:book:Documento on-line do guia do usuário do Slicer](./4.Slicing/readme.md)
- [:blue_book: Arquivo PDF do guia do usuário do Slicer](./4.Slicing/Slicing.pdf)

## <a id="a5"> 5. Firmware </a>
**:pencil: O que é o arquivo bin do firmware e o código-fonte?**
O arquivo bin do firmware é a memória exata gravada no flash incorporado.   
O código-fonte do firmware é a parte central do firmware. Nosso código-fonte de firmware é baseado em [**marlin**](https://www.marlinfw.org).
Você pode baixar o arquivo bin do firmware ou o código-fonte no link abaixo.   
- [:arrow_down: Arquivo bin de firmware][LINK_FIRMWARE]
- [:arrow_down: Código-fonte do firmware][LINK_SOURCECODE]

## <a id="a6"> 6. Solução de problemas </a>
Se você tiver algum problema ao instalar e usar a impressora, tente primeiro encontrar uma solução no [:book: Documento on-line de solução de problemas][LINK_TROUBLESHOOTING]. Se você não conseguir resolver este problema, entre em contato conosco por email (:email: support@zonestar3d.com).   

## <a id="a7"> 7. Imprimir peças </a>
Existem vários componentes na máquina que são impressos e também preparamos algumas atualizações para você. Se desejar, você pode baixá-los e imprimi-los e depois instalá-los em sua máquina.

-----
## <a id="a8"> Recursos opcionais </a>
Introduzimos alguns recursos opcionais para esta máquina. Você pode atualizar esses recursos a qualquer momento de acordo com suas preferências. Se você estiver interessado nisso, leia o guia de recursos de atualização opcionais para obter informações mais detalhadas.
- [:book: Documento on-line do guia de recursos de atualização opcionais][Z9V5MK6_OPTION]
- [:blue_book: arquivo pdf do guia de recursos de atualização opcional](./OptionalFeatures.pdf)

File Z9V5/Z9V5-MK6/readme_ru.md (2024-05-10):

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

----
## <a id="choose-language">:globe_with_meridians: Choose language </a>










----
# Руководство пользователя 3D-принтера ZONESTAR Z9V5Pro-MK6

----
## :warning: ПОЖАЛУЙСТА, ВНИМАНИЕ
#### :loudspeaker: Перед использованием аппарата внимательно прочтите [:book:"Меры предосторожности при использовании M4V6"][M4V6_PRECAUTION].
#### :loudspeaker: Необходимо загрузить 4 нити на горячую головку M4V6 одновременно. Неправильная работа может заблокировать горячую головку смешивания цветов. Если блокировка горячего конца вызвана неправильной эксплуатацией, гарантия не распространяется. О том, как загружать нити, см. в [:book: этом руководстве][Z9V5MK6_LOADFILAMENT].
#### :loudspeaker: Если вы новичок в использовании 3D-принтера, внимательно прочитайте [:book: Пошаговое руководство][Z9V5MK6_STEPBYSTEP] и выполните необходимые действия.
- [:book: **Меры предосторожности при использовании M4V6**][M4V6_PRECAUTION]
- [:book: **Как правильно загружать нити**][Z9V5MK6_LOADFILAMENT]
- [:book: **Пошаговое руководство**][Z9V5MK6_STEPBYSTEP]
<!-- - [:blue_book: PDF-файл с пошаговым руководством](./step_by_step.pdf) -->

------
## :book: Содержание
- [**Руководство по установке**](#a1)
- [**Руководство по эксплуатации**](#a2)
- [**Тестовые файлы gcode**](#a3)
- [**Программное обеспечение для нарезки**](#a4)
- [**Прошивка**](#a5)
- [**Устранение неполадок**](#a6)
- [**Печать файлов stl деталей**](#a7)
- [**Дополнительные функции обновления**](#a8)

-----
## <a id="a1"> 1. Руководство по установке </a>
Сначала ознакомьтесь со следующими документами и видеороликами, чтобы завершить установку и подключение машины.
### Монтаж
- [:book: Онлайн-документ с руководством по установке](./1.Installation/Installation.md)
- [:blue_book: Руководство по установке PDF-файл](./1.Installation/Installation.pdf)
- [:clapper: Видеоруководство по установке](https://youtu.be/TGHUVzV1Pg4)
### Проводка
- [:book: Онлайн-документ руководства по проводке](./1.Installation/Wiring.md)
- [:blue_book: PDF-файл руководства по подключению](./1.Installation/Wiring.pdf)
- [:art: Схема подключения](./1.Installation/Z9V5Pro_Wiring_Diagram.jpg)
- [:clapper: Видеоурок по подключению](https://youtu.be/tQQNLDOpdQU)

## <a id="a2"> 2. Руководство по эксплуатации </a>
### **Введение в ЖК-панель управления**
После завершения установки и подключения ознакомьтесь с приведенным ниже руководством, чтобы узнать, как использовать панель управления (ЖК-экран) и в целом понять функции ЖК-меню.
- [:book: Онлайн-документ ЖК-меню](./2.Operation/LCDMENU_Description.md)
- [:blue_book: PDF-файл ЖК-меню](./2.Operation/LCDMENU_Description.pdf)
#### **Распечатайте свои первые работы**
Теперь вы можете попробовать распечатать свои работы "Здравствуйте слово", перед тем как приступить к печати, вам сначала нужно сделать простую коррекцию высоты грядки (это называется "выравнивание грядки"), а затем загрузить нити в экструдер. (обратите внимание, что независимо от цвета вашего отпечатка вам необходимо загрузить в экструдеры и хот-энд все 4 нити). Затем вы можете вставить SD-карту в машину и выбрать на SD-карте файл gcode для тестирования 3D-модели. Более подробную информацию можно найти в документах ниже.
- [:book: Онлайн-документ руководства по эксплуатации](./2.Operation/Operation.md)
- [:blue_book: PDF-файл руководства по эксплуатации](./2.Operation/Operation.pdf)
#### :page_with_curl: Дополнительные возможности
Вы также можете прочитать следующие документы, чтобы получить более глубокое представление об экструдере (горячем конце и печатающей головке), используемом вашей машиной, а также о некоторых дополнительных функциях машины.
- [:book: Руководство по использованию функции «Смешать цвета»][LINK_MIX_FEATURE]
- [:book: Введение в хотэнд M4V6][LINK_M4V6]
- [:book: Печать с ПК](./2.Operation/PrintFromPC/readme.md)
- [:book: Руководство по использованию расширенных функций](./2.Operation/Advance_Features.md)

  ## <a id="a3"> 3. Проверка файла G-кода </a>
**:pencil: Что такое G-код в 3D-печати?**
G-код — это информация или инструкции, которые требуются 3D-принтеру для печати трехмерного объекта. Это язык, который 3D-принтер может понять. G-код генерируется вашим программным обеспечением для нарезки путем перевода стандартного файла 3D-моделирования, такого как STL, объекта, файла AMF и т. д. :page_with_curl: [**Ссылка 1**][GCODE_REF1] :page_with_curl: [**Ссылка 2**][GCODE_REF2]    
Мы сохранили несколько тестовых файлов gcode на SD-карте, чтобы проверить, правильно ли работает аппарат, или продемонстрировать, какие функции печати имеет этот аппарат. Если вы не можете найти файлы тестового gcode на SD-карте, загрузите их с [:arrow_down: **здесь**](./3.TestGcode/Test_gcode.zip).  
- **xyz_cube.gcode**: простой тестовый файл gcode, используемый для проверки правильности работы компьютера.
- **dog.gcode**: классический файл проверки качества печати.
- **Vase.gcode**: тестовая ваза.
   - **GradientMix_Vase.gcode**: ваза, аналогичная vase.gcode, но с включенной функцией «градиентного смешивания».
   - **RandomMix_Vase.gcode**: ваза, аналогичная vase.gcode, но с включенной функцией «случайного смешивания».
- **M4_4CTest.gcode**: тестовый файл базовых 4 цветов для 3D-принтера с горячим концом M4.
- **M4_4C_BODY3D.gcode**: более крупный тестовый файл с 4 цветами.
- **16color_tower.gcode**: тестовый файл базовых 16 цветов, показывающий результат смешивания нитей разных цветов.
- **level_test_310.gcode**: тестовый файл, используемый для проверки плоскостности горячего слоя (без автоматического выравнивания слоя).
- **level_test_310-G29.gcode**: тестовый файл, используемый для проверки плоскостности горячего слоя (с автоматическим выравниванием слоя).
**[:arrow_down: Загрузите дополнительные тестовые файлы gcode][M4_TEST_GCODE].**
 
## <a id="a4"> 4. Нарезка </a>
**[:pencil: Что такое нарезка в 3D-печати?](https://en.wikipedia.org/wiki/Slicer_(3D_printing))**
Слайсер — это программное обеспечение для создания траектории движения инструмента, используемое в большинстве процессов 3D-печати для преобразования объектной 3D-модели в конкретные инструкции для принтера. В частности, преобразование модели в формате STL в команды принтера в формате g-кода при производстве плавленых нитей и других подобных процессах.
- [:book:Интернет-документ руководства пользователя Slicer](./4.Slicing/readme.md)
- [:blue_book: PDF-файл руководства пользователя слайсера](./4.Slicing/Slicing.pdf)

## <a id="a5"> 5. Прошивка </a>
**:pencil: Что такое bin-файл прошивки и исходный код?**
bin-файл прошивки — это именно та память, которая записана во встроенную флэш-память.    
Исходный код прошивки является основной частью прошивки. Исходный код нашей прошивки основан на [**marlin**](https://www.marlinfw.org).
Вы можете скачать bin-файл прошивки или исходный код по ссылке ниже.   
- [:arrow_down: bin-файл прошивки][LINK_FIRMWARE]
- [:arrow_down: Исходный код прошивки][LINK_SOURCECODE]

## <a id="a6"> 6. Устранение неполадок </a>
Если у вас возникли проблемы с установкой и использованием принтера, попробуйте сначала найти решение в [:book: Интернет-документ по устранению неполадок][LINK_TROUBLESHOOTING]. Если вы не можете решить эту проблему, свяжитесь с нами по электронной почте (:email: support@zonestar3d.com).

## <a id="a7"> 7. Печать частей </a>
На машине есть несколько напечатанных компонентов, и мы также подготовили для вас некоторые обновления. Если хотите, вы можете скачать и распечатать их, а затем установить на свой компьютер.

-----
## <a id="a8"> Дополнительные функции </a>
Мы представили некоторые дополнительные функции для этой машины. Вы можете обновить эти функции в любое время в соответствии со своими предпочтениями. Если вас это интересует, прочтите Руководство по дополнительным функциям обновления, чтобы получить более подробную информацию.
- [:book: Онлайн-документ с руководством по функциям дополнительного обновления][Z9V5MK6_OPTION]
- [:blue_book: PDF-файл с руководством по дополнительным функциям обновления](./OptionalFeatures.pdf)

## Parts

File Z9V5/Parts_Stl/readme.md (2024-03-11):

## Print parts stl file of Z9V5
### Filament run out sensor
- :arrow_down:[**Case of filament run out sensor V6**](./FRODV6.zip)    
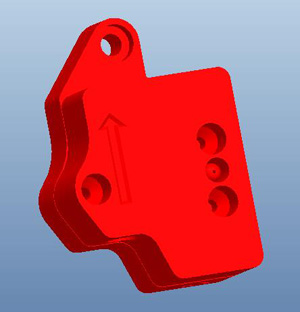
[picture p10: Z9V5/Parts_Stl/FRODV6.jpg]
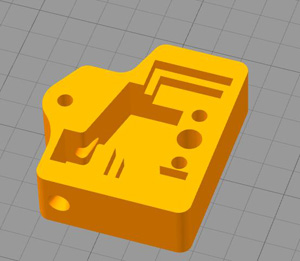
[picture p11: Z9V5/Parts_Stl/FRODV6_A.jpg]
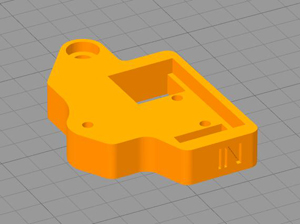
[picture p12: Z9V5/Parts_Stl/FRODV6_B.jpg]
       
:pushpin: If your machine is upgraded to Dual Gear Extruders, you need to update the FROD base prints, please download the stl from above link, print it out and replace them. stl file name: "FRODV6L-B.stl" and "FRODV6R-B.stl".      
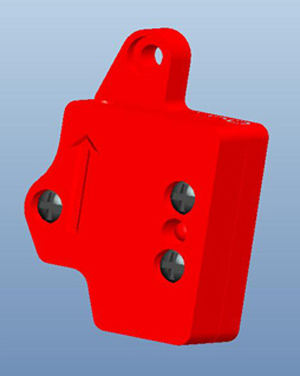
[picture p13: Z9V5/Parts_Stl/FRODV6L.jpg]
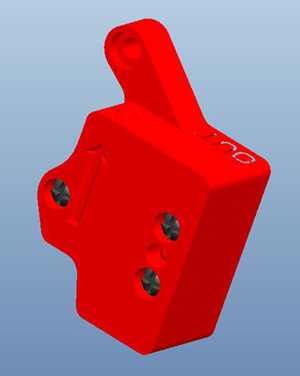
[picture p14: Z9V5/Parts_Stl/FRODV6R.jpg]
      

### hotend fan duct 
The hotend fan duck stl file to improve the effeciency of cooling.    
<!-- - [:arrow_down:**E4 hotend fan duct**](./fanduct_e4.zip)    
- [:arrow_down:**M4V4 hotend fan duct**](./fanduct_M4V4.zip)   
- [:arrow_down:**M4V6 hotend fan duct**](./fanduct_m4v6.zip)    -->
- [:arrow_down:**Fan duct for E4&M4 hotend**](./fanduct_4c_v7.zip)   
<!-- ![](fan_duck.jpg)  ![](fan_duck_m4.jpg)  ![](fanduct_m4v6.jpg)   -->
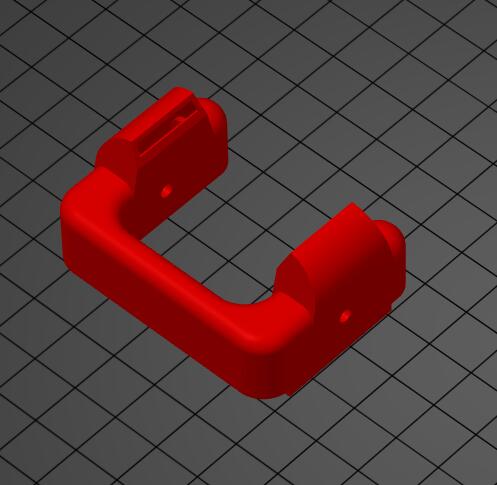
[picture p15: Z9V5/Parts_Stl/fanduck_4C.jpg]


### Hotend Cable Bracket
- [:arrow_down:**Hotend Cable Bracket**](./z9v5_hecable_holder.zip)   
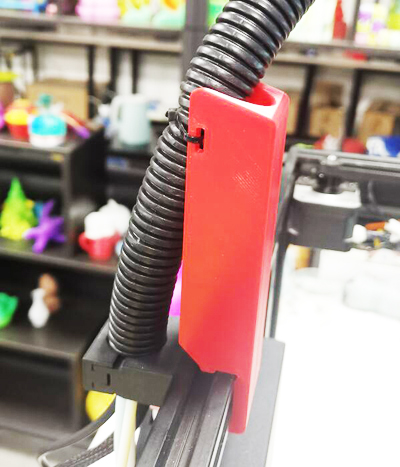
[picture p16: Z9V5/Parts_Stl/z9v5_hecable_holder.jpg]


### Bracket of ZL-Sensor(Only used on Z9V5Pro-MK3)
- [:arrow_down:**Bracket to mount ZL-Sensor**](./br_zlsensor.zip)    
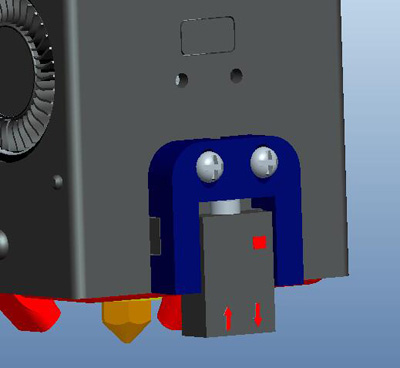
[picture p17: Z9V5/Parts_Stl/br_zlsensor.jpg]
  

### Recyclebin
A box (Installed  on the z-axis aluminum profile at the front left) to collect filament flowed out from the nozzle.     
- [:arrow_down:**Filament recyclebin box**](Recyclebin.zip)    


### tool supports  
- [:arrow_down:**Support for the tools**](./Z9_tool_supports.zip)    


### Filament Spool Bracket
- [:arrow_down:**FilamentSpoolBracket**](./FilamentSpoolBracket.zip)   


### Anti-entanglement Filament
- [:arrow_down:**Anti-entanglement Filament**](./antientanglementfilament.st)   


-----
### Made by customers
- [**Z9V5 Spool Holder by MichaW**](https://www.thingiverse.com/thing:4977619)
- [**Z9V5 Purge chute and nozzle clean by AFelix**](https://www.thingiverse.com/thing:4940319)
- [**Z9V5 Fan duct by Memphisrain**](https://www.thingiverse.com/thing:5754401)

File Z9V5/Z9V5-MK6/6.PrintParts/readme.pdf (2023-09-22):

readme.md | 2023-09-22

## Parts_Stl

Filament holder. (https://github.com/ZONESTAR3D/Z9/tree/main/Z9V5/Parts_Stl/FilamentSpoolBracket.zip) The filament holder of Z9V5Pro can support the vast majority of filament spool in the market, but there are also some filament spools that may be longer. You can download stl files and print them to replace the original ones.


Power supply fan cover. (https://github.com/ZONESTAR3D/Z9/tree/main/Z9V5/Parts_Stl/PSUfancover.zip) The fan of the power supply may have some dust after long-term use. You can print a cover and install it on the power fan, which can be easier to clean. And this cover can also reduce the noise of the fan.

Hotend fan duct. (https://github.com/ZONESTAR3D/Z9/tree/main/Z9V5/Parts_Stl/fanduct_m4v6.zip) The dock of the extruder fan is may be damaged after using a while, you can download and print one to replace it.


Filament recycling box. (https://github.com/ZONESTAR3D/Z9/tree/main/Z9V5/Parts_Stl/Recyclebin.zip) When printing, there are always some fine threads that need to be removed. It is a good idea to print a small garbage box and install it on the Z-axis profile of the machine to collect this garbage.


Tool station. (https://github.com/ZONESTAR3D/Z9/tree/main/Z9V5/Parts_Stl/Z9_tool_supports.zip) Diagonal pliers, tweezers, shovels, and small screwdrivers are commonly used tools with 3D printers. You can print a collection station for tools to place them.


Filament run out detector case. (https://github.com/ZONESTAR3D/Z9/tree/main/Z9V5/Parts_Stl/FRODV6.zip) The case of the Filament run our sensor equipped with the machine is a print part. If it is damaged, you can print one by yourself.


More print stl files, please refer to https://github.com/ZONESTAR3D/Z9/tree/main/Z9V5/Parts_Stl.

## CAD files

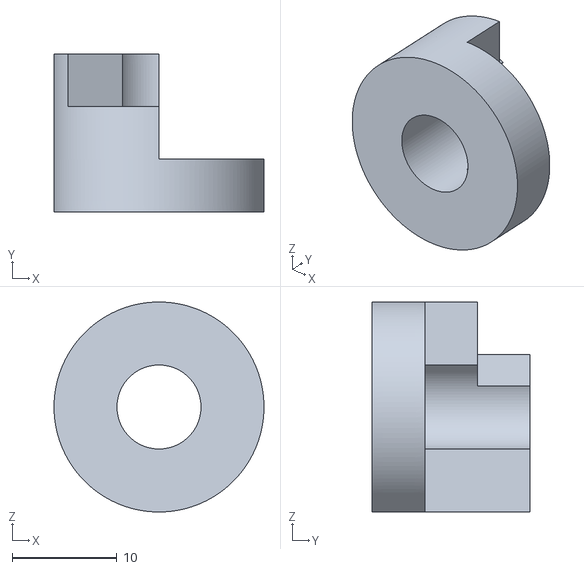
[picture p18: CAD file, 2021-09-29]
Z9M3/Z9F/3. Test gcode/3 Color/3c_test/stl/3c_test_1.stl
20.0 x 15.0 x 20.0

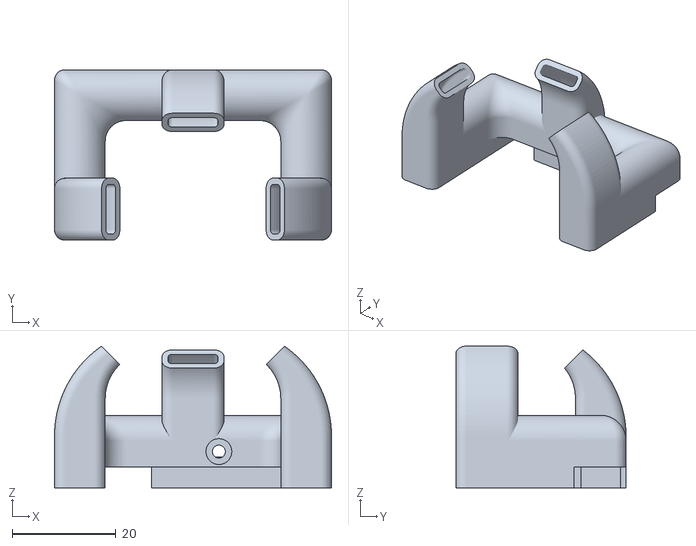
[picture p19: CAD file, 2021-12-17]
Z9M3/Z9F/4. Print Parts stl/fanduck_m3_v4.stl
53.5 x 32.9 x 27.4

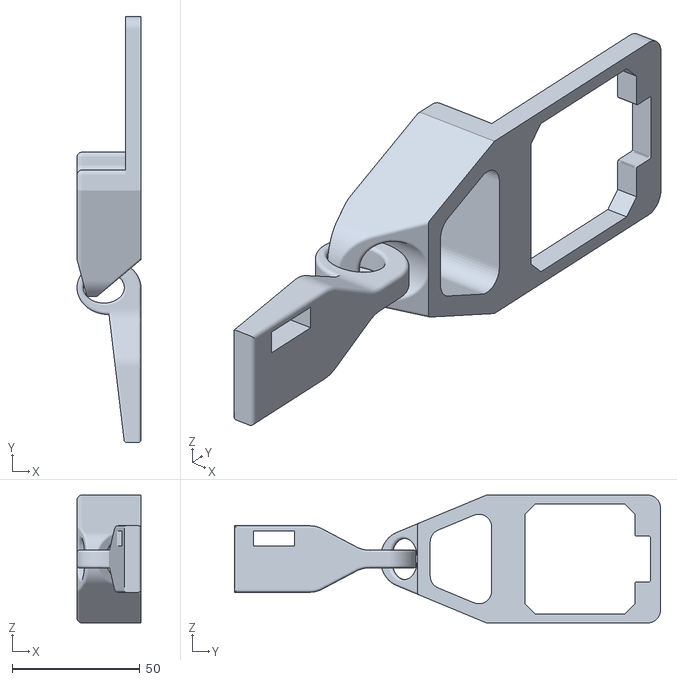
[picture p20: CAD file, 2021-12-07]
Z9M3/Z9F/4. Print Parts stl/FROD bracket/z9_frod_br.stl
25.0 x 166.5 x 50.0

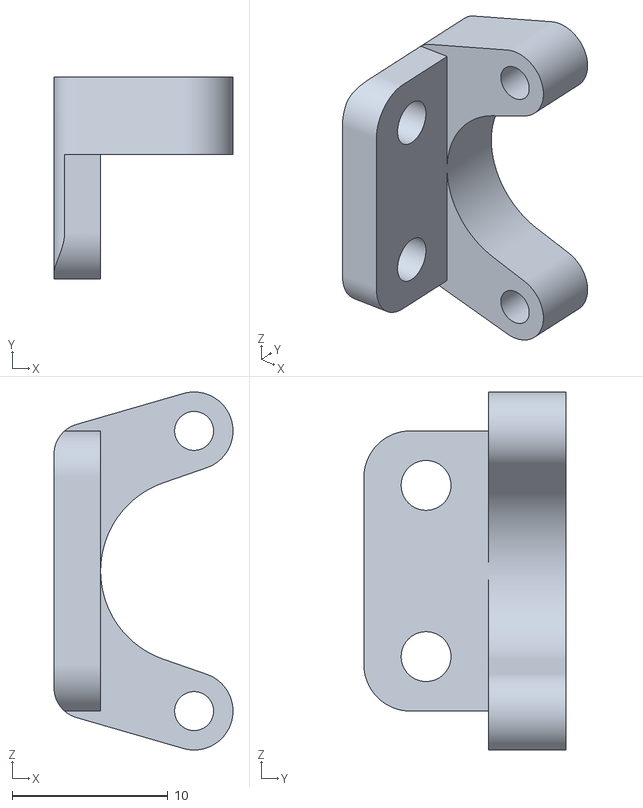
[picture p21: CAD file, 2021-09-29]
Z9M3/Z9T/6. Upgrade Feature/BL-Touch/BLtouch_Bracket.STL
11.5 x 13.0 x 23.0

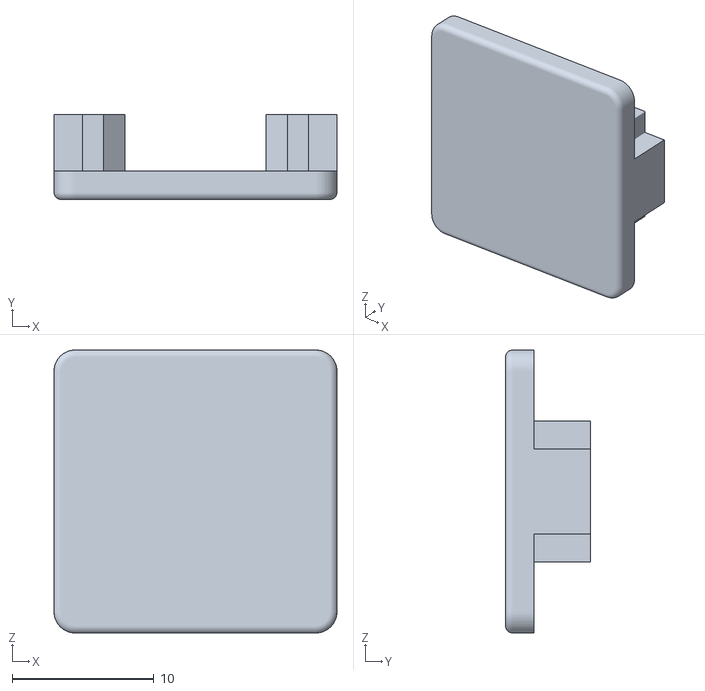
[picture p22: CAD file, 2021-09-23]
Z9M4/6. Print Parts/cap_af_20v.stl
20.0 x 6.00 x 20.0

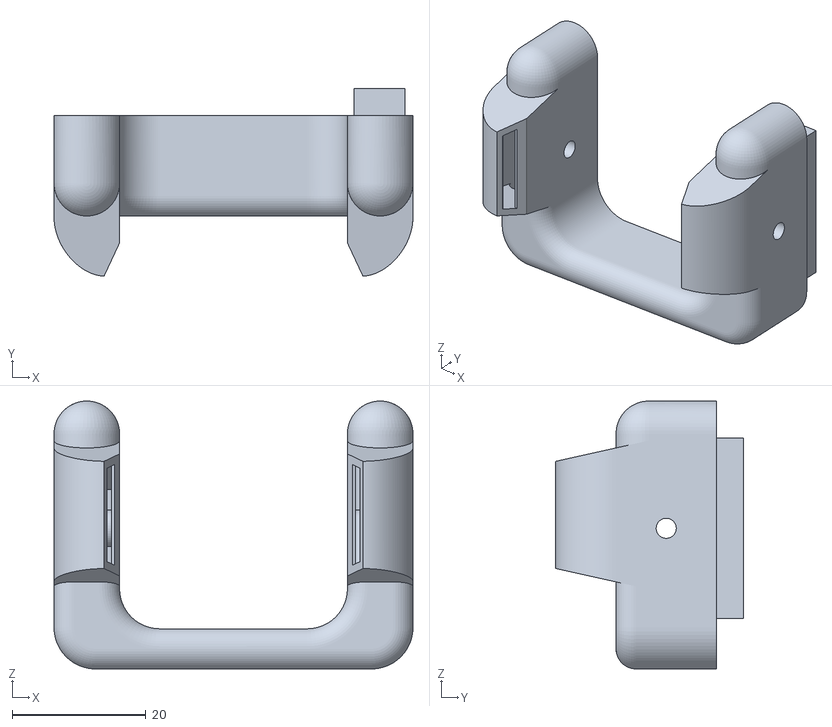
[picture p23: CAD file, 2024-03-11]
Z9V5/Parts_Stl/fanduct_4c_v7.stl
53.6 x 28.0 x 40.0

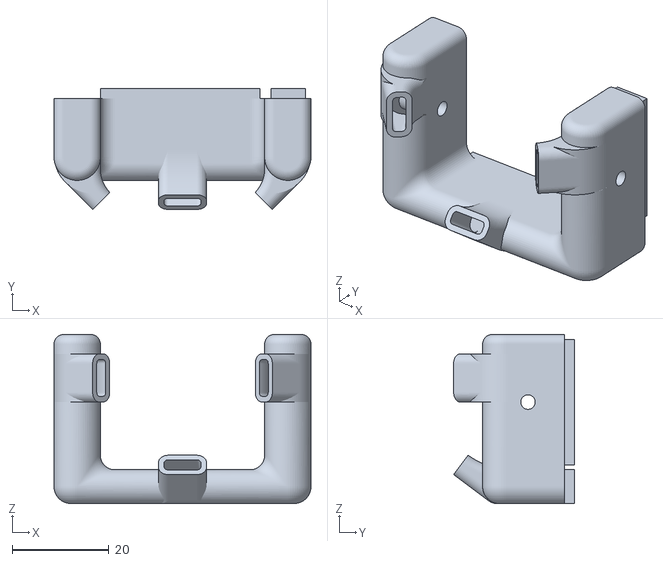
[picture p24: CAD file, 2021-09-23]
Z9V5/Z9V5_FAQ/Issue_of_strings_drawing_m4/fan_duck_m4_v3.stl
53.2 x 25.0 x 35.0

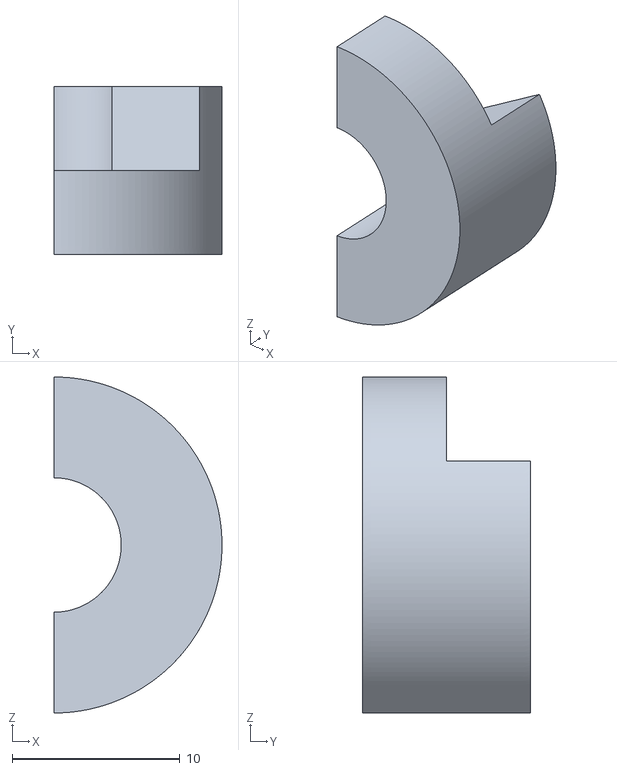
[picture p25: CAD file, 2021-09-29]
Z9M3/Z9F/3. Test gcode/3 Color/3c_test/stl/3c_test_2.stl
10.0 x 10.0 x 20.0

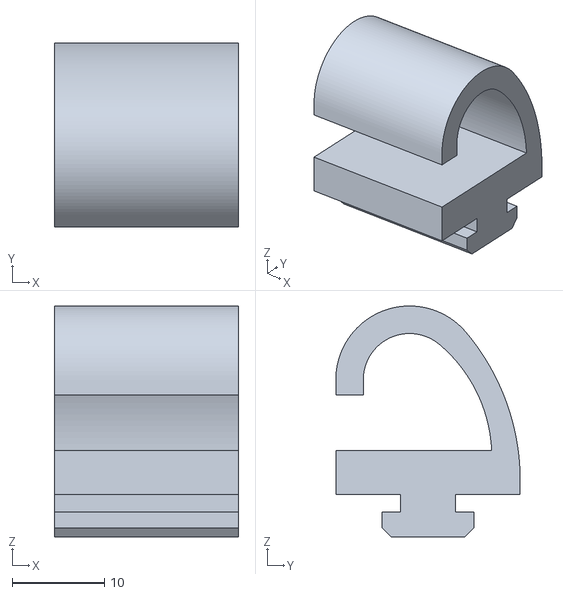
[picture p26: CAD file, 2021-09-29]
Z9M3/Z9F/4. Print Parts stl/wire_clip2.stl
20.0 x 20.0 x 25.0

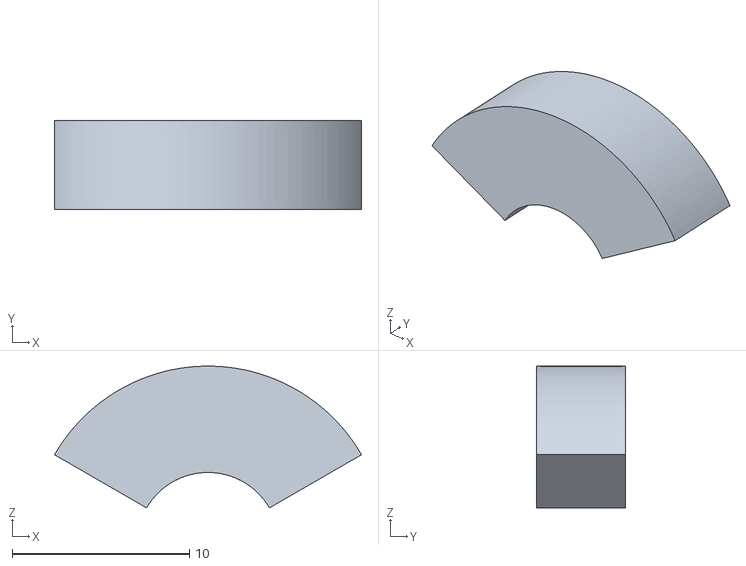
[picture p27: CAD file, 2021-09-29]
Z9M3/Z9T/3. Test gcode/3 Color/3c_test/stl/3c_test_3.stl
17.3 x 5.00 x 8.00

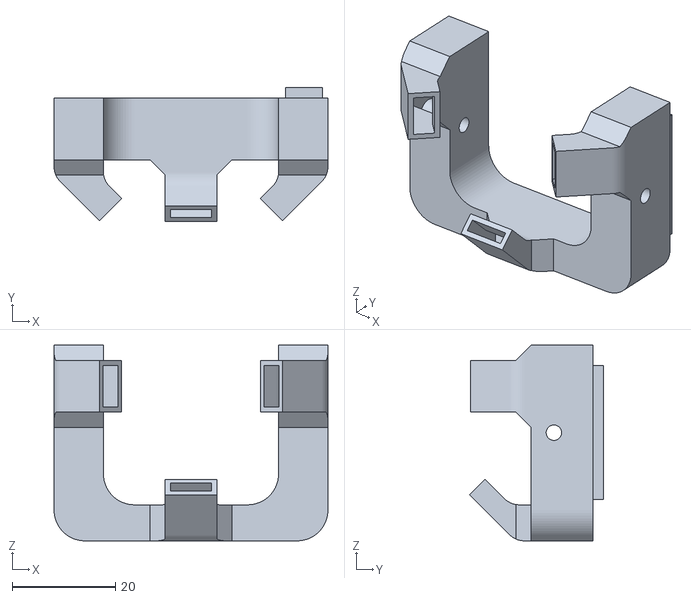
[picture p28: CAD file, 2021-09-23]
Z9M4/6. Print Parts/fanduck_m4_v3.stl
53.2 x 25.9 x 38.0

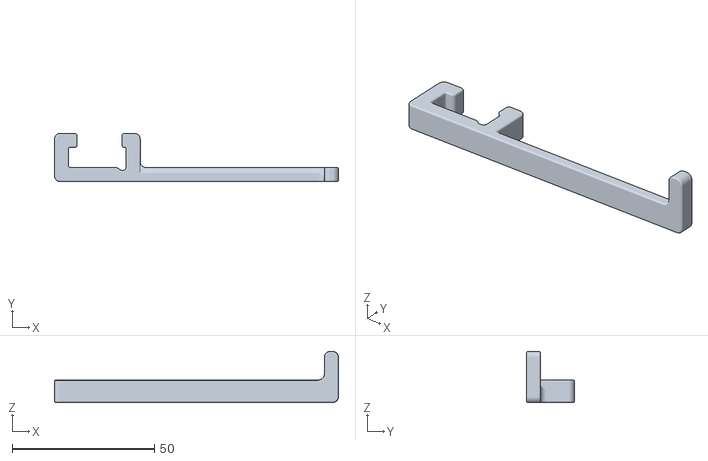
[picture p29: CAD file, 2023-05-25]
Z9V5/Parts_Stl/antifilamententanglement.stl
100.0 x 17.0 x 18.0

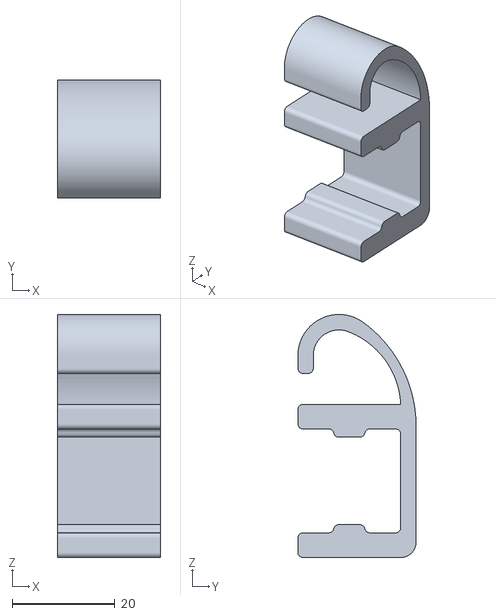
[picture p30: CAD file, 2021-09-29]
Z9M3/Z9F/4. Print Parts stl/wire_clip.stl
20.0 x 23.0 x 47.3

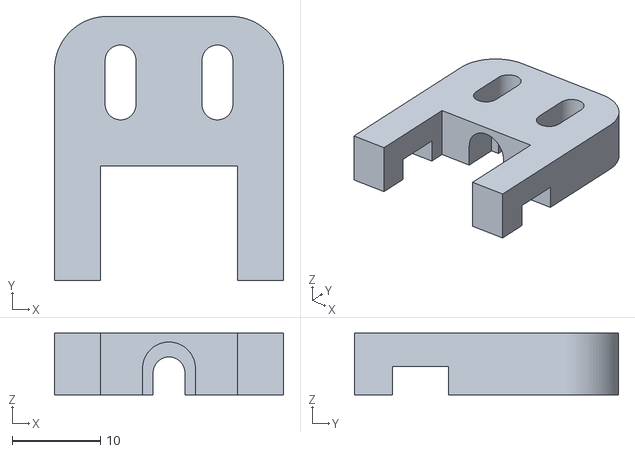
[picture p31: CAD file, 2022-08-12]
Z9V5/Parts_Stl/br_zlsensor_v2.stl
26.0 x 30.0 x 7.00

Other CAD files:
Z9M3/Z9F/4. Print Parts stl/lcd12864_case.stl
Z9M3/Z9T/4. Print Parts stl/lcd12864_case.stl
Z9M4/6. Print Parts/lcd12864_case_v2.stl
Z9V5/Parts_Stl/br_zlsensor_v1.stl
Z9V5/Z9V5-MK1/4.Test gcode/8 Color/8c_test.3mf
Z9V5/Z9V5-MK1/4.Test gcode/8 Color/stl/8c_0.stl
Z9V5/Z9V5-MK1/4.Test gcode/8 Color/stl/8c_1.stl
Z9V5/Z9V5-MK1/4.Test gcode/8 Color/stl/8c_2.stl
Z9V5/Z9V5-MK1/4.Test gcode/8 Color/stl/8c_3.stl
Z9V5/Z9V5-MK1/4.Test gcode/8 Color/stl/8c_4.stl
Z9V5/Z9V5-MK1/4.Test gcode/8 Color/stl/8c_5.stl
Z9V5/Z9V5-MK1/4.Test gcode/8 Color/stl/8c_6.stl
Z9V5/Z9V5-MK1/4.Test gcode/8 Color/stl/8c_7.stl
Z9V5/Z9V5-MK1/4.Test gcode/8 Color/stl/8c_8.stl
Z9V5/Z9V5-MK1/4.Test gcode/Mix Color/Vase.stl
Z9V5/Z9V5-MK2/7. Others/Auto Bed Leveling/BLtouch/BLtouch_Bracket.STL
Z9V5/Z9V5-MK2/7. Others/Direct Drive Extrruder/stl/ENDSTOP_TG_Z6.stl
Z9V5/Z9V5-MK2/7. Others/Direct Drive Extrruder/stl/TPUEXT_PC_V0.stl
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

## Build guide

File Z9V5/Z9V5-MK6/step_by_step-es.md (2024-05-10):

[LCD_MENU]: https://github.com/ZONESTAR3D/Z9/tree/main/Z9V5/Z9V5-MK6/LCDMENU_Description.md
[PRUSA_SLICER]: https://github.com/ZONESTAR3D/Slicing-Guide/tree/master/PrusaSlicer
[VIDEO_POWERON]: https://github.com/ZONESTAR3D/Z9/assets/29502731/02fa8e57-a292-4aa5-bb7b-eaa703e3fc1b
[VIDEO_BEDLEVEL]: https://youtu.be/jNf98S0u2VQ
[VIDEO_LOADFILAMENT]: https://youtu.be/1rr4dXRxKc4
[VIDEO_PRINT1C]: https://youtu.be/NbVy8NjKt_s
[VIDEO_PRINT4C]: https://youtu.be/iddKadfrdjw

----
## <a id="choose-language">:globe_with_meridians: Choose language </a>










----
## Guía paso por paso
En una palabra, desde el momento en que recibe la máquina hasta el momento en que puede imprimir su propio archivo de modelo 3D, se requieren un total de 5 pasos: **Instalación - Nivelación de la cama - Cargar filamentos - Imprimir el archivo gcode de prueba - Cortar y Imprima su propio archivo 3D**.
#### Instalación (Igual que Z9V5-MK5)
(https://www.youtube.com/watch?v=pdr8nLl3T3w)
#### Operaciones básicas
(https://www.youtube.com/watch?v=GrCOZ4ADHeA)
#### Impresión multicolor
(https://www.youtube.com/watch?v=iddKadfrdjw)

### <a id ="a1">Paso 1. Instalación</a>
- 1.1 **Instalación**. Consulte el [:book: **guía de instalación**](./1.Installation/Installation.md) y el [:clapper: **tutorial de instalación en vídeo**](https://youtu.be/pdr8nLl3T3w) para completar la instalación de la máquina.
- 1.2 **Cableado**. El proceso de cableado consiste básicamente en introducir el enchufe en el enchufe correspondiente. Lo que debe prestar atención es **asegurarse de que los conectores estén bien enchufados**, especialmente para los enchufes de acoplamiento de 2 pines. Además, para el cableado del cabezal de impresión (extremo caliente), tenga en cuenta que hay varios enchufes del mismo pero de diferentes colores; preste atención para enchufarlos según el color del enchufe.
- 1.3 **Encendido**. Cuando se complete el cableado, puede [:clapper: **encender Z9V5**][VIDEO_POWERON]. Tenga en cuenta en particular que el Z9V5 tiene 2 interruptores de alimentación. uno es ***interruptor de CA*** (el interruptor rojo en la parte posterior de la máquina) y otro es ***interruptor de CC*** (un interruptor de botón redondo de metal en la parte frontal de la caja de control de la máquina), primero debe encender el interruptor de CA y luego **mantener presionado** el interruptor de CC durante aproximadamente 5 segundos para encender Z9V5.
- 1.4 **Simplemente prueba**. Después del encendido, puede operar el menú en la pantalla LCD ([:book: **LCD Menu description**](./2.Operation/LCDMENU_Description.md)) para verificar si la máquina puede funcionar normalmente. Normalmente esto implica varios pasos:
   - 1.4.1 **Preparar>>Inicio automático>>Inicio todo**. Este paso es para hacer que el cabezal de impresión de la máquina regrese al origen.
   - 1.4.2 **Preparar>>Temperatura>>Precalentar PLA**. Este paso es para verificar que el extremo caliente y la cama caliente se puedan calentar normalmente. En este paso, cuando la temperatura de la boquilla excede los 60 grados, debería ver un ventilador en el lado derecho del cabezal de impresión (extremo caliente) girar. , este es el ventilador de refrigeración del extremo caliente.
   - 1.4.3 **Preparar>>Temperatura>>Velocidad del VENTILADOR:**. Después de presionar la perilla y configurar la velocidad del ventilador (establecida en 255), ahora también debería poder subir el ventilador (en el lado izquierdo para el hotend M4V6).
   Después de estos 3 pasos, básicamente se determina que la máquina está funcionando normalmente, puede continuar con los siguientes pasos. Si descubre que alguna pieza no funciona correctamente, verifique nuevamente el cableado o consulte [:clapper: **vídeotutorial de prueba automática de la máquina**](https://youtu.be/Mf92BlmKA0A) para realizar una máquina automática. pruebas.

### <a id ="a2">Paso 2. Nivelar la cama</a>
Antes de comenzar a imprimir, debe realizar una simple nivelación de la cama para establecer la altura entre la boquilla y la cama (plataforma de impresión), de modo que el filamento se pueda pegar bien en la cama. Consulte [:clapper: **Videotutorial de nivelación de la cama**][VIDEO_BEDLEVEL] para hacerlo.

### <a id ="a3">Paso 3. Cargar filamentos</a>
Consulte este [:clapper: vídeo tutorial][VIDEO_LOADFILAMENT] para cargar los 4 filamentos en las extrusoras y el extremo caliente.
#### :warning: ATENCIÓN POR FAVOR :warning:
1. **Necesita cargar los 4 filamentos en el extremo caliente, independientemente de lo que imprima en un color o en impresiones 3D de varios colores.**
2. **Asegúrese de que los filamentos se hayan cargado hasta la parte inferior del extremo caliente; de lo contrario, podría bloquear el extremo caliente.**

### <a id ="a4">Paso 4. Imprima el archivo gcode de prueba</a>
Las impresoras 3D FDM solo pueden reconocer archivos gcode; debe copiar los archivos gcode a la tarjeta SD, insertar la tarjeta SD en el zócalo para tarjetas SD de la impresora 3D y luego comenzar a imprimir.
Dado que Z9V5Pro es una impresora 3D con 4 extrusoras, le sugerimos que imprima un modelo 3D de un color y un modelo 3D de 4 colores para probar si la máquina funciona correctamente.
#### Imprimir impresiones 3D de un color
##### [:clapper: vídeo tutorial][VIDEO_PRINT1C]
- **Preparar archivo gcode**. Localice el archivo **xyz_cube.gcode** de su tarjeta SD o [:arrow_down: haga clic aquí para descargarlo](./3.Test_gcode/xyz_cube.zip) y descomprímalo en su PC, y luego copie el archivo **xyz_cube .gcode** a la tarjeta SD, conecte la tarjeta SD al conector SD de la máquina.
- **Imprimir desde tarjeta SD**. Mueva el cursor al elemento **Imprimir** en la pantalla LCD y haga clic en la perilla y elija el archivo **xyz_cube**, haga clic en la perilla para comenzar a imprimir.
- **Ajuste la altura de la boquilla**. Espere a que se calienten la boquilla y la cama, y cuando comience a imprimir la primera capa, haga doble clic en la perilla de la pantalla LCD y ajuste la distancia desde la boquilla hasta la cama (la boquilla es más alta que la etiqueta adhesiva aproximadamente 0,4 mm), espere hasta que finalice la impresión. finalizado.
#### Imprimir impresiones 3D en 4 colores
##### [:clapper: vídeo tutorial][VIDEO_PRINT4C]
- **Preparar archivo gcode**. Localice el archivo **M4_4CTest.gcode** de su tarjeta SD o [:arrow_down: haga clic aquí para descargarlo](./3.Test_gcode/M4_4CTest.zip) y descomprímalo en su PC, y luego copie el archivo **M4_4CTest .gcode** a la tarjeta SD, conecte la tarjeta SD al conector SD de la máquina.
- **Imprimir desde tarjeta SD**. Mueva el cursor al elemento **Imprimir** en la pantalla LCD, haga clic en la perilla y elija el archivo **M4_4CTest**, haga clic en la perilla para comenzar a imprimir.
- **Ajuste la altura de la boquilla**. Espere a que se calienten la boquilla y la cama, y cuando comience a imprimir la primera capa, haga doble clic en la perilla de la pantalla LCD y ajuste la distancia desde la boquilla hasta la cama (la boquilla es más alta que la etiqueta adhesiva aproximadamente 0,4 mm), espere hasta que finalice la impresión. finalizado.

### <a id ="a5">Paso 5. Corta tu propio modelo 3D e imprímelo</a>
Antes de imprimir sus propios modelos 3D, necesita convertir el archivo del modelo 3D (un archivo de formato stl/obj/AMF [descargado de Internet](#a6) o dibujado por usted mismo) a un archivo gcode, este proceso se llama < u>"**rebanar**"</u>.
- En primer lugar, debe descargar el software de corte e instalarlo en su computadora, y configurar los parámetros de su máquina en el software de corte o cargar el archivo preestablecido de su máquina establecido por el fabricante de la impresora 3D.
- A continuación, debe ejecutar el software de corte y es posible que también deba establecer algunos parámetros de acuerdo con las características de su archivo de modelo 3D y luego ejecutar el corte.
- Una vez finalizado el corte, copie el archivo gcode generado en la tarjeta SD y siga el [:point_right:Stpe 4](#a4) para imprimirlo en su impresora 3D.
#### *PrusaSlicer* es el software de corte que recomendamos; consulte [:point_right:aquí][PRUSA_SLICER] para descargar e instalar el software PrusaSlicer y leer la guía del usuario.
:warning: **ATENCIÓN POR FAVOR** :warning:     
El Z9V5Pro-MK6 predeterminado está equipado con un hotend M4V6 (mezcla de colores 4 en 1, salida), preste atención para elegir el ajuste preestablecido de la impresora (Z9 + M4 Hotend) al cortar.

----
### <a id ="a6">Sitios web famosos de descarga gratuita de modelos 3D</a>
- [thingiverse](https://www.thingiverse.com/)  
- [printables](https://www.printables.com/)  
- [youmagine](https://www.youmagine.com/)   

----

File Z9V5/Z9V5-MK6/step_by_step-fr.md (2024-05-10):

[LCD_MENU]: https://github.com/ZONESTAR3D/Z9/tree/main/Z9V5/Z9V5-MK6/LCDMENU_Description.md
[PRUSA_SLICER]: https://github.com/ZONESTAR3D/Slicing-Guide/tree/master/PrusaSlicer
[VIDEO_POWERON]: https://github.com/ZONESTAR3D/Z9/assets/29502731/02fa8e57-a292-4aa5-bb7b-eaa703e3fc1b
[VIDEO_BEDLEVEL]: https://youtu.be/jNf98S0u2VQ
[VIDEO_LOADFILAMENT]: https://youtu.be/1rr4dXRxKc4
[VIDEO_PRINT1C]: https://youtu.be/NbVy8NjKt_s
[VIDEO_PRINT4C]: https://youtu.be/iddKadfrdjw

----
## <a id="choose-language">:globe_with_meridians: Choose language </a>










----
## Guide étape par étape
En un mot, à partir du moment où vous recevez la machine jusqu'au moment où vous pouvez imprimer votre propre fichier de modèle 3D, 5 étapes au total sont requises : **Installation - Mise à niveau du lit - Chargement des filaments - Impression du fichier gcode de test - Tranchage et imprimez votre propre fichier 3D**.
#### Installation (identique à Z9V5-MK5)
(https://www.youtube.com/watch?v=pdr8nLl3T3w)
#### Opérations de base
(https://www.youtube.com/watch?v=GrCOZ4ADHeA)
#### Impression multicolore
(https://www.youtube.com/watch?v=iddKadfrdjw)

### <a id ="a1">Étape 1. Installation</a>
- 1.1 **Installation**. Reportez-vous au [:book: **guide d'installation**](./1.Installation/Installation.md) et au [:clapper: **tutoriel vidéo d'installation**](https://youtu.be/pdr8nLl3T3w) pour terminer l'installation de la machine.
- 1.2 **Câblage**. le processus de câblage consiste essentiellement à insérer la fiche dans la prise correspondante. Ce à quoi vous devez faire attention, c'est **pour vous assurer que les connecteurs sont bien branchés**, en particulier pour les prises d'accueil à 2 broches. De plus, pour le câblage de la tête d'impression (hot end), veuillez noter qu'il existe plusieurs prises identiques mais de couleurs différentes, veuillez faire attention à les brancher en fonction de la couleur de la prise.
- 1.3 **Mise sous tension**. Une fois le câblage terminé, vous pouvez [:clapper: **allumer le Z9V5**][VIDEO_POWERON]. A noter notamment que le Z9V5 dispose de 2 interrupteurs d'alimentation. l'un est un ***interrupteur AC*** (l'interrupteur rouge à l'arrière de la machine) et un autre est un ***interrupteur DC*** (un interrupteur à bouton-poussoir rond en métal à l'avant du boîtier de commande de la machine), vous devez d'abord allumer l'interrupteur AC, puis **appuyer et maintenir** l'interrupteur DC pendant environ 5 secondes pour allumer le Z9V5.
- 1.4 **Testez simplement**. Après la mise sous tension, vous pouvez utiliser le menu sur l'écran LCD ([:book: **LCD Menu description**](./2.Operation/LCDMENU_Description.md)) pour vérifier si la machine peut fonctionner normalement. Cela implique généralement plusieurs étapes :
   - 1.4.1 **Préparer>>Accueil Auto>>Accueil Tout**. Cette étape consiste à faire revenir la tête d'impression de la machine à l'origine.
   - 1.4.2 **Préparation>>Température>>Préchauffer le PLA**. Cette étape consiste à vérifier l'extrémité chaude et le lit chaud peut être chauffé normalement. Dans cette étape, lorsque la température de la buse dépasse 60 degrés, vous devriez voir un ventilateur sur le côté droit de la tête d'impression (extrémité chaude) tourner. , c'est le ventilateur de refroidissement de l'extrémité chaude.
   - 1.4.3 **Préparation>>Température>>Vitesse du VENTILATEUR :**. Après avoir appuyé sur le bouton et réglé la vitesse du ventilateur (réglée sur 255), vous devriez maintenant pouvoir augmenter le ventilateur (sur le côté gauche pour le hotend M4V6).
   Après ces 3 étapes, il est essentiellement déterminé que la machine fonctionne normalement, vous pouvez passer aux étapes suivantes. Si vous constatez qu'une pièce ne fonctionne pas correctement, veuillez vérifier le câblage ou vous référer à[:clapper: **Tutoriel vidéo de test automatique de la machine**](https://youtu.be/Mf92BlmKA0A) pour faire une machine automatique essai.

### <a id ="a2">Étape 2. Mise à niveau du lit</a>
Avant de commencer l'impression, vous devez effectuer un simple nivellement du lit pour régler la hauteur entre la buse et le lit (plate-forme d'impression), afin que le filament puisse bien être collé sur le lit. Veuillez vous référer à [:clapper: **Tutoriel vidéo sur la mise à niveau du lit**][VIDEO_BEDLEVEL] pour le faire.

### <a id ="a3">Étape 3. Charger les filaments</a>
Référez-vous à ce [:clapper: tutoriel vidéo][VIDEO_LOADFILAMENT] pour charger les 4 filaments dans les extrudeuses et la hot end.
#### :warning: ATTENTION S'IL VOUS PLAÎT :warning:
1. **Vous devez charger les 4 filaments jusqu'à l'extrémité chaude, que vous imprimiez une couleur ou des impressions 3D multicolores.**
2. **Assurez-vous que les filaments ont été chargés jusqu'au bas de l'extrémité chaude, sinon cela pourrait bloquer l'extrémité chaude.**

### <a id ="a4">Étape 4. Imprimer le fichier gcode de test</a>
Les imprimantes 3D FDM ne peuvent reconnaître que les fichiers gcode, vous devez copier les fichiers gcode sur la carte SD, insérer la carte SD dans la prise pour carte SD de l'imprimante 3D, puis commencer à imprimer.
La Z9V5Pro étant une imprimante 3D dotée de 4 extrudeuses, nous vous suggérons d'imprimer un modèle 3D une couleur et un modèle 3D 4 couleurs pour tester si la machine fonctionne correctement.
#### Imprimer des impressions 3D en une seule couleur
##### [:clapper: tutoriel vidéo][VIDEO_PRINT1C]
- **Préparer le fichier gcode**. Localisez le fichier **xyz_cube.gcode** sur votre carte SD ou [:arrow_down: cliquez ici pour le télécharger](./3.Test_gcode/xyz_cube.zip) et décompressez-le sur votre PC, puis copiez le **xyz_cube .gcode** sur la carte SD, branchez la carte SD sur la prise SD de la machine.
- **Imprimer depuis la carte SD**. Déplacez le curseur sur l'élément **Imprimer** sur l'écran LCD, cliquez sur le bouton et choisissez le fichier **xyz_cube**, cliquez sur le bouton pour lancer l'impression.
- **Régler finement la hauteur de la buse**. Attendez le chauffage de la buse et du lit chaud, et lorsque vous commencez à imprimer la première couche, double-cliquez sur le bouton de l'écran LCD et ajustez la distance entre la buse et le lit (la buse est plus haute que l'autocollant d'environ 0,4 mm), attendez que l'impression soit terminée. fini.
#### Imprimer des impressions 3D en 4 couleurs
##### [:clapper: tutoriel vidéo][VIDEO_PRINT4C]
- **Préparer le fichier gcode**. Localisez le fichier **M4_4CTest.gcode** sur votre carte SD ou [:arrow_down: cliquez ici pour le télécharger](./3.Test_gcode/M4_4CTest.zip) et décompressez-le sur votre PC, puis copiez le **M4_4CTest. .gcode** sur la carte SD, branchez la carte SD sur la prise SD de la machine.
- **Imprimer depuis la carte SD**. Déplacez le curseur sur l'élément **Imprimer** sur l'écran LCD, cliquez sur le bouton et choisissez le fichier **M4_4CTest**, cliquez sur le bouton pour lancer l'impression.
- **Régler finement la hauteur de la buse**. Attendez le chauffage de la buse et du lit chaud, et lorsque vous commencez à imprimer la première couche, double-cliquez sur le bouton de l'écran LCD et ajustez la distance entre la buse et le lit (la buse est plus haute que l'autocollant d'environ 0,4 mm), attendez que l'impression soit terminée. fini.

### <a id ="a5">Étape 5. Découper votre propre modèle 3D et l'imprimer</a>
Avant d'imprimer vos propres modèles 3D, vous devez convertir le fichier de modèle 3D (un fichier au format stl/obj/AMF qui [téléchargé depuis Internet](#a6) ou dessiné par vous-même) en un fichier gcode, ce processus est appelé < u>"**tranchage**"</u>.
- Tout d'abord, vous devez télécharger le logiciel de découpage et l'installer sur votre ordinateur, puis définir les paramètres de votre machine dans le logiciel de découpage ou charger le fichier prédéfini de votre machine défini par le fabricant de l'imprimante 3D.
- Ensuite, vous devez exécuter le logiciel de découpage, et vous devrez peut-être également définir certains paramètres en fonction des caractéristiques de votre fichier de modèle 3D, puis exécuter le découpage.
- Une fois le découpage terminé, copiez le fichier gcode généré sur la carte SD et suivez la [:point_right:Stpe 4](#a4) pour l'imprimer par votre imprimante 3D.
#### *PrusaSlicer* est le logiciel de découpage que nous avons recommandé, veuillez vous référer à [:point_right:here][PRUSA_SLICER] pour télécharger et installer le logiciel PrusaSlicer et lire le guide de l'utilisateur.
:warning: **ATTENTION S'IL VOUS PLAÎT** :warning:    
Le Z9V5Pro-MK6 par défaut est équipé d'une extrémité chaude M4V6 (4-IN-1-OUT mix Color), veuillez faire attention à choisir le préréglage de l'imprimante (Z9 + M4 Hotend) lors du découpage.

----
### <a id ="a6">Célèbres sites de téléchargement de modèles 3D gratuits</a>
- [thingiverse](https://www.thingiverse.com/)  
- [printables](https://www.printables.com/)  
- [youmagine](https://www.youmagine.com/)   

----

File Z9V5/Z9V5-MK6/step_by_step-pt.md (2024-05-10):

[LCD_MENU]: https://github.com/ZONESTAR3D/Z9/tree/main/Z9V5/Z9V5-MK6/LCDMENU_Description.md
[PRUSA_SLICER]: https://github.com/ZONESTAR3D/Slicing-Guide/tree/master/PrusaSlicer
[VIDEO_POWERON]: https://github.com/ZONESTAR3D/Z9/assets/29502731/02fa8e57-a292-4aa5-bb7b-eaa703e3fc1b
[VIDEO_BEDLEVEL]: https://youtu.be/jNf98S0u2VQ
[VIDEO_LOADFILAMENT]: https://youtu.be/1rr4dXRxKc4
[VIDEO_PRINT1C]: https://youtu.be/NbVy8NjKt_s
[VIDEO_PRINT4C]: https://youtu.be/iddKadfrdjw

----
## <a id="choose-language">:globe_with_meridians: Choose language </a>










----
## Guia passo a passo
Em uma palavra, desde o momento em que você recebeu a máquina até o momento em que você pode imprimir seu próprio arquivo de modelo 3D, são necessárias 5 etapas no total: **Instalação - Nivelamento da cama - Carregar filamentos - Imprimir arquivo gcode de teste - Fatiar e imprima seu próprio arquivo 3D**.
#### Instalação (igual ao Z9V5-MK5)
(https://www.youtube.com/watch?v=pdr8nLl3T3w)
#### Operações básicas
(https://www.youtube.com/watch?v=GrCOZ4ADHeA)
#### Impressão multicolorida
(https://www.youtube.com/watch?v=iddKadfrdjw)

### <a id ="a1">Etapa 1. Instalação</a>
- 1.1 **Instalação**. Consulte o [:book: **guia de instalação**](./1.Installation/Installation.md) e [:clapper: **tutorial em vídeo de instalação**](https://youtu.be/pdr8nLl3T3w) para conclua a instalação da máquina.
- 1.2 **Fiação**. o processo de fiação consiste basicamente em inserir o plugue na tomada correspondente. O que você precisa prestar atenção é **certificar-se de que os conectores estão bem encaixados**, especialmente para os soquetes de acoplamento de 2 pinos. Além disso, para a fiação da cabeça de impressão (hot end), observe que existem vários soquetes da mesma cor, mas de cores diferentes, preste atenção para conectá-los de acordo com a cor do soquete.
- 1.3 **LIGAR**. Quando a fiação estiver concluída, você pode [:clapper: **ligar o Z9V5**][VIDEO_POWERON]. Observe em particular que o Z9V5 possui 2 interruptores liga / desliga. um é o ***interruptor AC*** (o interruptor vermelho na parte traseira da máquina) e o outro é o ***interruptor DC*** (um botão redondo de metal na frente da caixa de controle da máquina), você precisa ligar o interruptor CA primeiro e depois **pressionar e segurar** o interruptor CC por cerca de 5 segundos para ligar o Z9V5.
- 1.4 **Simplesmente teste**. Depois de ligar, você pode operar o menu na tela LCD ([:book: **LCD Menu description**](./2.Operation/LCDMENU_Description.md)) para verificar se a máquina pode funcionar normalmente. Geralmente isso envolve várias etapas:
   - 1.4.1 **Preparar>>Auto Home>>Home All**. Esta etapa serve para fazer com que o cabeçote de impressão da máquina retorne à origem.
   - 1.4.2 **Preparar>>Temperatura>>Pré-aquecer PLA**. Esta etapa é verificar se a extremidade quente e a cama quente podem ser aquecidas normalmente. Nesta etapa, quando a temperatura do bico exceder 60 graus, você deverá ver um ventilador no lado direito da cabeça de impressão (extremidade quente) girando. , este é o ventilador de resfriamento hot end.
   - 1.4.3 **Preparar>>Temperatura>>Velocidade do VENTILADOR:**. Depois de pressionar o botão e definir a velocidade do ventilador (definida para 255), agora você também poderá aumentar o ventilador (no lado esquerdo do hotend M4V6).
   Após essas 3 etapas, é basicamente determinado que a máquina está funcionando normalmente, você pode prosseguir para as etapas seguintes. Se você achar que alguma peça não está funcionando corretamente, verifique novamente a fiação ou consulte [:clapper: **tutorial em vídeo de teste automático de máquina**](https://youtu.be/Mf92BlmKA0A) para fazer uma máquina automática testando.

### <a id ="a2">Etapa 2. Nivelamento da cama</a>
Antes de iniciar a impressão, é necessário fazer um simples nivelamento da cama para definir a altura entre o bico e a mesa (plataforma de impressão), para que o filamento possa ficar bem colado na mesa. Consulte [:clapper: **Tutorial em vídeo sobre nivelamento da cama**][VIDEO_BEDLEVEL] para fazer isso.

### <a id ="a3">Etapa 3. Carregar filamentos</a>
Consulte este [:clapper: vídeo tutorial][VIDEO_LOADFILAMENT] para carregar todos os 4 filamentos nas extrusoras e no hot end.
#### :warning: ATENÇÃO POR FAVOR :warning:
1. **Você precisa carregar todos os 4 filamentos no hot end, independentemente de imprimir em uma cor ou em impressões 3D multicoloridas.**
2. **Certifique-se de que os filamentos foram carregados na parte inferior da extremidade quente, caso contrário, isso pode causar o bloqueio da extremidade quente.**

### <a id ="a4">Etapa 4. Imprimir arquivo gcode de teste</a>
As impressoras 3D FDM só podem reconhecer arquivos gcode, você precisa copiar os arquivos gcode para o cartão SD, inserir o cartão SD no soquete do cartão SD da impressora 3D e então começar a imprimir.
Como a Z9V5Pro é uma impressora 3D com 4 extrusoras, sugerimos que você imprima um modelo 3D de uma cor e um modelo 3D de 4 cores para testar se a máquina está funcionando corretamente.
#### Imprima impressões 3D em uma cor
##### [:clapper: vídeo tutorial][VIDEO_PRINT1C]
- **Prepare o arquivo gcode**. Localize o arquivo **xyz_cube.gcode** em seu cartão SD ou [:arrow_down: clique aqui para baixá-lo](./3.Test_gcode/xyz_cube.zip) e descompacte-o em seu PC e copie o arquivo **xyz_cube .gcode** para cartão SD, conecte o cartão SD ao soquete SD da máquina.
- **Imprimir do cartão SD**. Mova o cursor para o item **Imprimir** na tela LCD e clique no botão e escolha o arquivo **xyz_cube**, clique no botão para iniciar a impressão.
- **Ajuste a altura do bico**. Aguarde o aquecimento do bico e do viveiro, e ao iniciar a impressão da primeira camada, clique duas vezes no botão da tela LCD e ajuste a distância do bico à base (o bico é superior ao adesivo cerca de 0,4 mm), aguarde até que a impressão seja finalizado.
#### Imprimir impressões 3D em 4 cores
##### [:clapper: vídeo tutorial][VIDEO_PRINT4C]
- **Prepare o arquivo gcode**. Localize o arquivo **M4_4CTest.gcode** em seu cartão SD ou [:arrow_down: clique aqui para baixá-lo](./3.Test_gcode/M4_4CTest.zip) e descompacte-o em seu PC e copie o **M4_4CTest.zip .gcode** para cartão SD, conecte o cartão SD ao soquete SD da máquina.
- **Imprimir do cartão SD**. Mova o cursor para o item **Imprimir** na tela LCD e clique no botão e escolha o arquivo **M4_4CTest**, clique no botão para iniciar a impressão.
- **Ajuste a altura do bico**. Aguarde o aquecimento do bico e do viveiro, e ao iniciar a impressão da primeira camada, clique duas vezes no botão da tela LCD e ajuste a distância do bico à base (o bico é superior ao adesivo cerca de 0,4 mm), aguarde até que a impressão seja finalizado.

### <a id ="a5">Etapa 5. Fatiar seu próprio modelo 3D e imprimi-lo</a>
Antes de imprimir seus próprios modelos 3D, você precisa converter o arquivo do modelo 3D (um arquivo no formato stl/obj/AMF que [baixado da internet](#a6) ou desenhado por você mesmo) em um arquivo gcode, este processo é chamado < u>"**cortando**"</u>.
- Primeiramente você precisa baixar o software de fatiamento e instalá-lo em seu computador, e definir os parâmetros de sua máquina no software de fatiamento ou carregar o arquivo predefinido de sua máquina definido pelo fabricante da impressora 3D.
- Em seguida, você precisa executar o software de fatiamento, podendo também definir alguns parâmetros de acordo com as características do seu arquivo de modelo 3D e então executar o fatiamento.
- Após terminar o fatiamento, copie o arquivo gcode gerado para o cartão SD e siga o [:point_right:Stpe 4](#a4) para imprimi-lo em sua impressora 3D.
#### *PrusaSlicer* é o software de fatiamento que recomendamos. Consulte [:point_right:here][PRUSA_SLICER] para baixar e instalar o software PrusaSlicer e ler o guia do usuário.
:warning: **ATENÇÃO POR FAVOR** :warning:     
Z9V5Pro-MK6 padrão equipado com um hot end M4V6 (4-IN-1-OUT mix Color), preste atenção para escolher a predefinição da impressora (Z9 + M4 Hotend) ao fatiar.

----
### <a id ="a6">Sites famosos para download gratuito de modelos 3D</a>
- [thingiverse](https://www.thingiverse.com/)  
- [printables](https://www.printables.com/)  
- [youmagine](https://www.youmagine.com/)   
----

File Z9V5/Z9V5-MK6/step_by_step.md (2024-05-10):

[LCD_MENU]: https://github.com/ZONESTAR3D/Z9/tree/main/Z9V5/Z9V5-MK6/LCDMENU_Description.md
[PRUSA_SLICER]: https://github.com/ZONESTAR3D/Slicing-Guide/tree/master/PrusaSlicer
[VIDEO_POWERON]: https://github.com/ZONESTAR3D/Z9/assets/29502731/02fa8e57-a292-4aa5-bb7b-eaa703e3fc1b
[VIDEO_BEDLEVEL]: https://youtu.be/jNf98S0u2VQ
[VIDEO_LOADFILAMENT]: https://youtu.be/1rr4dXRxKc4
[VIDEO_PRINT1C]: https://youtu.be/NbVy8NjKt_s
[VIDEO_PRINT4C]: https://youtu.be/iddKadfrdjw

----
## <a id="choose-language">:globe_with_meridians: Choose language </a>










----
## Step by Step Guide
In a word, from the moment you received the machine to the moment you can print your own 3D model file, there are a total of 5 steps required: **Installation - Leveling the bed - Load filaments - Printing test gcode file - Slicing and print your own 3d file**.      
#### Installation (Same as Z9V5-MK5)
(https://www.youtube.com/watch?v=pdr8nLl3T3w)
#### Basic Operations
(https://www.youtube.com/watch?v=GrCOZ4ADHeA)
#### Multi-color printing
(https://www.youtube.com/watch?v=iddKadfrdjw)

### <a id ="a1">Step 1. Installation</a>
- 1.1 **Installation**. Refer to the [:book: **installation guide**](./1.Installation/Installation.md) and [:clapper: **installation video tutorial**](https://youtu.be/pdr8nLl3T3w) to complete the installation of the machine.
- 1.2 **Wiring**. the process of wiring is basically to insert the plug into the corresponding socket. What you need to pay attention is **to make sure the connectors are plug well**, especially for the 2PIN docking sockets. In addition, for the wiring of the print head (hot end), please note that there are several sockets of the same but different colors, please pay attention to plug them according to the color of the socket.
- 1.3 **Power ON**. When wiring is complete, you can [:clapper: **turn on Z9V5**][VIDEO_POWERON]. Please note in particular that the Z9V5 has 2 power switches. the one is ***AC switch***(the red switch on the back of the machine) and another is ***DC switch***(a round metal push button switch on the front of the machine control box), you need to turn on the AC switch first and then **press and hold** the DC switch for about 5 seconds to turn on Z9V5.
- 1.4 **Simply Test**. After power on, you can operate the menu on the LCD screen ([:book: **LCD Menu description**](./2.Operation/LCDMENU_Description.md)) to verify whether the machine can work normally. Usually this involves several steps:
  - 1.4.1 **Prepare>>Auto Home>>Home All**. This step is to make the print head of the machine return to the origin.
  - 1.4.2 **Prepare>>Temperature>>Preheat PLA**. This step is to check the hot end and the hot bed can be heated normally.In this step, when the temperature of the nozzle exceeds 60 degrees, you should see a fan on the right side of the print head (hot end) spin up, this is the hot end cooling fan. 
  - 1.4.3 **Prepare>>Temperature>>FAN Speed:**. After pressing the knob and setting the fan speed (set to 255), you should now be able to turn the fan (on left side for M4V6 hotend) up as well.     
  After these 3 steps, it is basically determined that the machine are working normally, you can proceed to the following steps. If you find that any part is not working properly, please double check the wiring, or refer to[:clapper: **machine auto testing video tutorial**](https://youtu.be/Mf92BlmKA0A) to do a auto machine testing.

### <a id ="a2">Step 2. Leveling the bed</a>
Before start printing, you need to do a simple bed leveling to set the height between the nozzle and the bed (printing platform), so that the filament can be pasted on the bed well. Please refer to [:clapper: **Bed leveling video tutorial**][VIDEO_BEDLEVEL] to do it.

### <a id ="a3">Step 3. Load filaments</a>
Refer to this [:clapper: video tutorial][VIDEO_LOADFILAMENT] to load all 4 filaments to the extruders and hot end.     
#### :warning: ATTENTION PLEASE :warning: 
1. **You need load all 4 filaments to the hot end whatever you print one color or multi color 3d prints.**
2. **Ensure the filaments has been loaded to the bottom of the hot end, otherwise it may cause blockage the hot end.**

### <a id ="a4">Step 4. Print test gcode file</a>
FDM 3D printers can only recognize gcode files, you need to copy the gcode files to the SD card, insert the SD card into the SD card socket of the 3D printer, and then start to print.    
Since Z9V5Pro is a 3D printer with 4 extruders, we suggest that you print a one color 3d model and a 4 colors 3d model to test whether the machine is working properly.
#### Print one color 3d prints
##### [:clapper: Video Tutorial][VIDEO_PRINT1C]
- **Prepare gcode file**. Locate the **xyz_cube.gcode** file from your SD card or [:arrow_down: click here to download it](./3.TestGcode/Test_gcode.zip) and unzip it on your PC, and then copy the **xyz_cube.gcode** to SD card, plug the SD card to the machine's SD socket.
- **Print from SD card**. Move cursor to **Print** item on LCD screen and click the knob and choose **xyz_cube** file, click knob to start printing.
- **Fine tune nozzle height**. Wait the nozzle and hotbed heating, and when starting to print the first layer, double click the knob of LCD screen and fine tune the distance from the nozzle to the bed (nozzle is higher than sticker about 0.4mm), wait until the printing is finished.
#### Print 4 color 3d prints
##### [:clapper: Video Tutorial][VIDEO_PRINT4C]
- **Prepare gcode file**. Locate the **M4_4CTest.gcode** file from your SD card or [:arrow_down: click here to download it](./3.TestGcode/M4_4C_test.zip) and unzip it on your PC, and then copy the **M4_4CTest.gcode** to SD card, plug the SD card to the machine's SD socket.
- **Print from SD card**. Move cursor to **Print** item on LCD screen and click the knob and choose **M4_4CTest** file, click knob to start printing.
- **Fine tune nozzle height**. Wait the nozzle and hotbed heating, and when starting to print the first layer, double click the knob of LCD screen and fine tune the distance from the nozzle to the bed (nozzle is higher than sticker about 0.4mm), wait until the printing is finished.

### <a id ="a5">Step 5. Slicing your own 3d model and print it</a>
Before printing your own 3D models, you need to convert the 3d model file (a stl/obj/AMF format file which [downloaded from the internet](#a6) or drawing by yourself) to a gcode file, this process is called <u>"**slicing**"</u>. 
- Firstly you need to download the slicing software and install it on your computer, and set the parameters of your machine in the slicing software or load the preset file of your machine which set by the 3d printer manufacture.   
- Next, you need to run the slicing software, and may also need to set some parameters according to the characteristics of your 3D model file and then execute slicing. 
- After slicing finished, copy the generated gcode file to the SD card and following the [:point_right:Stpe 4](#a4) to print it out by your 3d printer.   
#### *PrusaSlicer* is the slicing software we recommended, please refer to [:point_right:here][PRUSA_SLICER] to download and install PrusaSlicer software and read the user guide. 
:warning: **ATTENTION PLEASE** :warning:     
Default Z9V5Pro-MK6 equipied with a M4V6 (4-IN-1-OUT mix Color) hot end, please pay attention to choose the printer preset (Z9 + M4 Hotend) when slicing.     

----
### <a id ="a6">Famous free 3D model download websites</a>
- [thingiverse](https://www.thingiverse.com/)  
- [printables](https://www.printables.com/)  
- [youmagine](https://www.youmagine.com/)   

----

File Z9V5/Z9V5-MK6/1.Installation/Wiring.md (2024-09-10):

# Z9V5-MK6 wiring guide

----
## [:clapper: Wiring video tutorial](https://youtu.be/tQQNLDOpdQU)

----
## Electronics parts
#### Please refer to the following figure to understand the location and name of the electronic components of the machine.
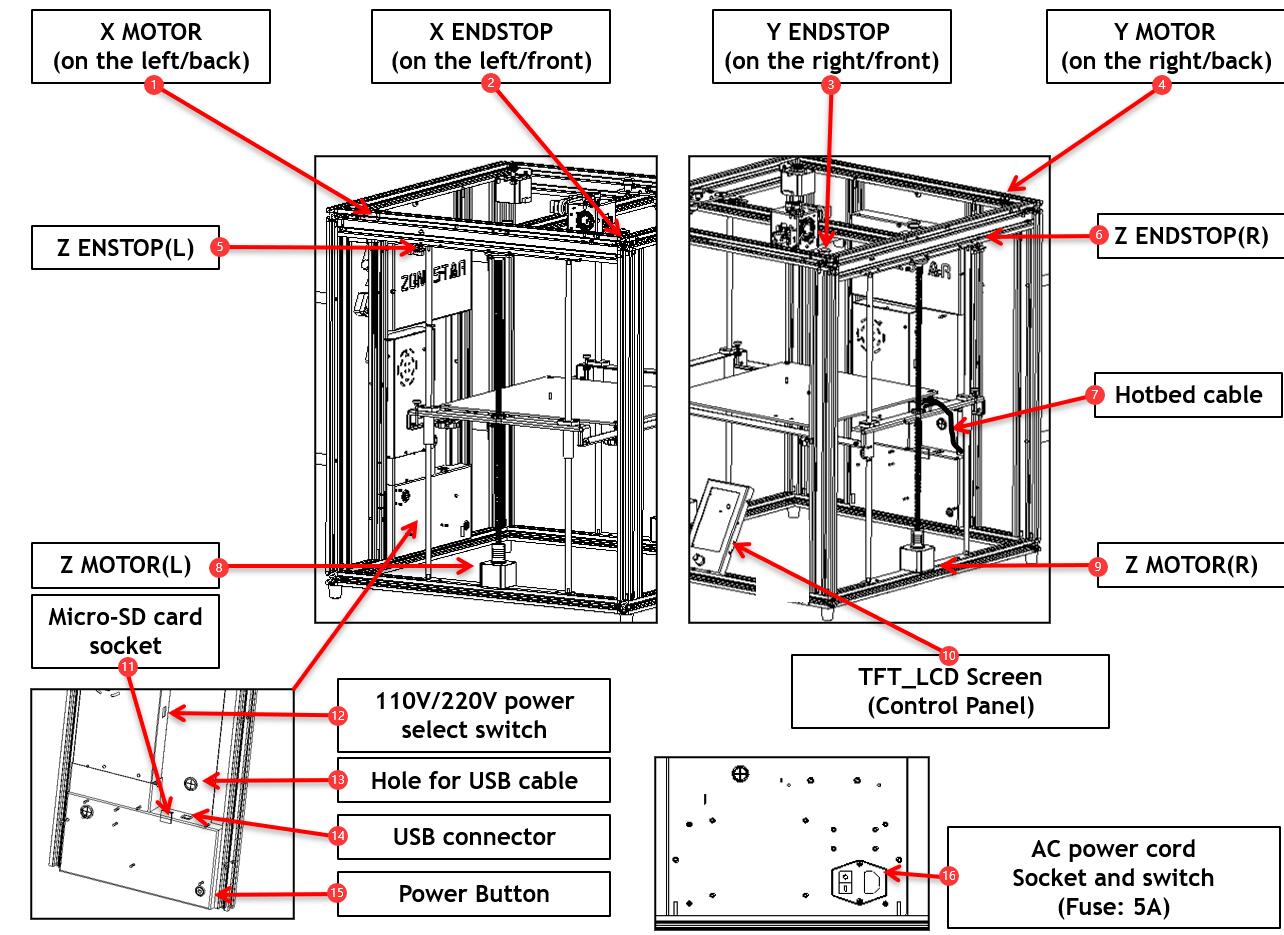
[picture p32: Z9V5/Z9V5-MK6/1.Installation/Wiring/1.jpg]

>
     1. X motor (on the left/back) 2. X ENDSTOP (on the left/front) 3. Y ENDSTOP (on the right/front)  4. Y motor (on the right/back)
     5. Left Z ENDSTOP             6. Right Z ENDSTOP               7. Cable for Heat bed              8. Left Z motor                       
     9. Right Z motor             10. LCD Screen (Control Panel)   11. Micro-SD card socket           12. 110V/220V power select switch
    13. Hole for USB cable        14. USB connector                15. DC Power Button                16. AC power socket and switch

## Wiring Diagram
#### Plug the wiring connector to the connectors of the electronic component as shown in the following figure, incude:
- **X motor wire and X ENDSTOP**
- **Y motor wire and Y ENDSTOP**
- **Left and right Z motor wire and Z ENDSTOP**
- **Hot bed cable (power and temperature sensor)**
- **LCD screen**
- **Hot end assembly (*Note: Hot end wires has already connected before the kit leaving factory.*)**
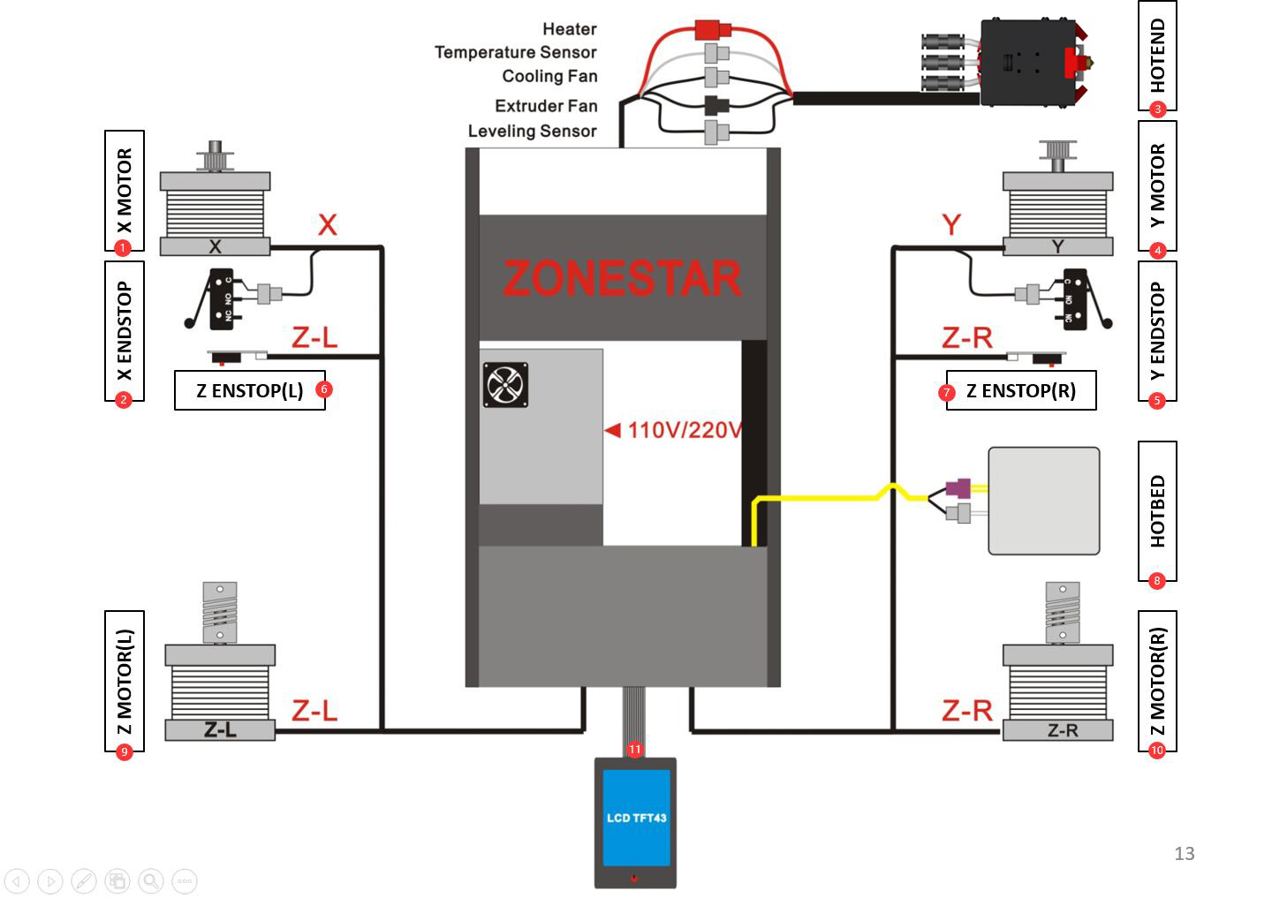
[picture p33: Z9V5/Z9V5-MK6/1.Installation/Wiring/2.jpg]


## Layout the wires
#### Put the wires to the profile grooves, cover with profile plastics strips. Tie the wires to the profiles after connected.
#### :warning: Be careful not to damage the insulation of wires when puting the motor cables to the profile grooves.
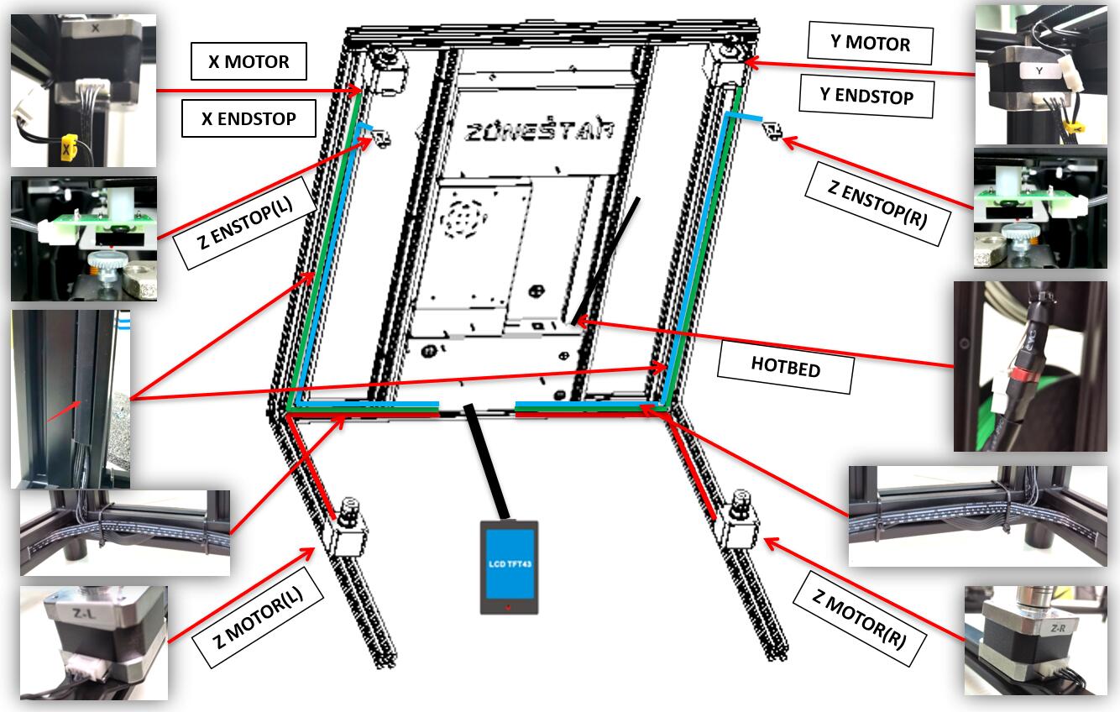
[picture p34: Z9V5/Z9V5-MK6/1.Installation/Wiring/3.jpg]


## Confirm the wiring
### Confirm all wires are properly connected to the connectors.
#### Confirm the X/Y axis move smoothly by moving the "print head" manually.
#### Confirm the motor shaft has fixed with the lead screws properly by rotating both of the Z couplings manually.
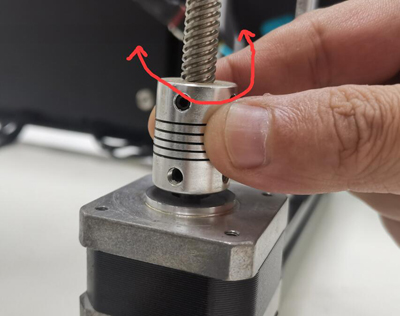
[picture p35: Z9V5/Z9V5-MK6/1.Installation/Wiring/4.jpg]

#### Confirm the Z-axis limit switch adjustment knob and the hot bed screw have been adjusted to the specified position.
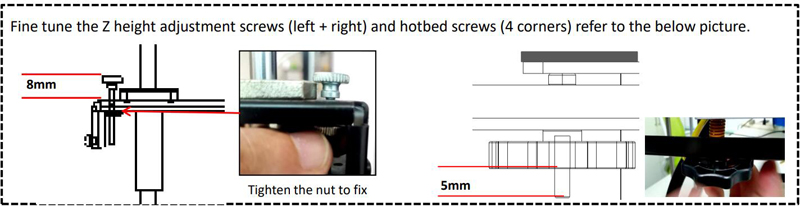
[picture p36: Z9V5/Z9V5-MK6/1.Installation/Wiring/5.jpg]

#### :warning:Confirm the AC voltage select switch of the power supply has been set to the correct position.
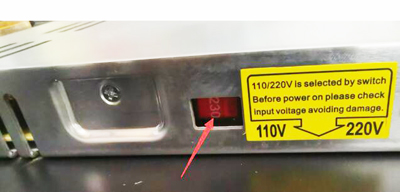
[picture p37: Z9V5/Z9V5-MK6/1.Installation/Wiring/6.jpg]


## Power on the machine
#### 1. Connect one end of the power cord (female base) to the printer, and then connect the other end of the power cord to your power outlet. Turn on the AC power switch of the 3d printer.
#### 2. Push and hold the DC power button, until you can see the LCD shows "logo screen", release the DC power button.
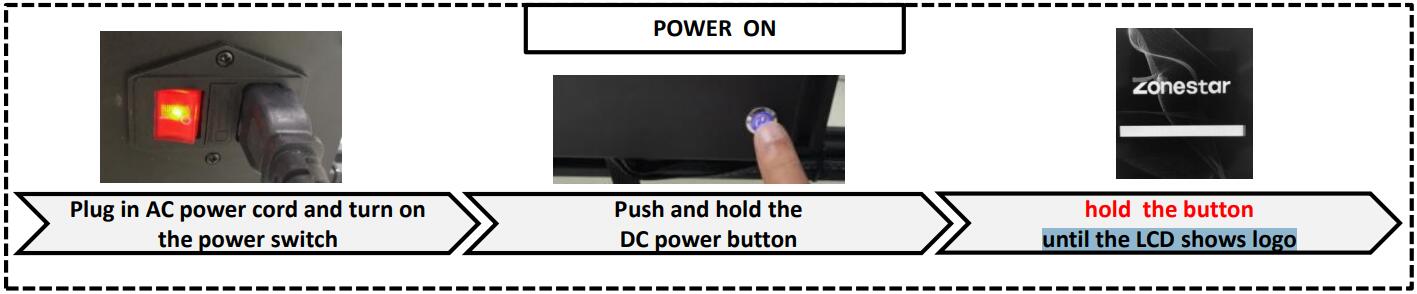
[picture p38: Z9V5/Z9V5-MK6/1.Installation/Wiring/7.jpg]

##### Tips: If you need to power off the printer, please turn off the printer on LCD screen first and then turn off the AC power switch.
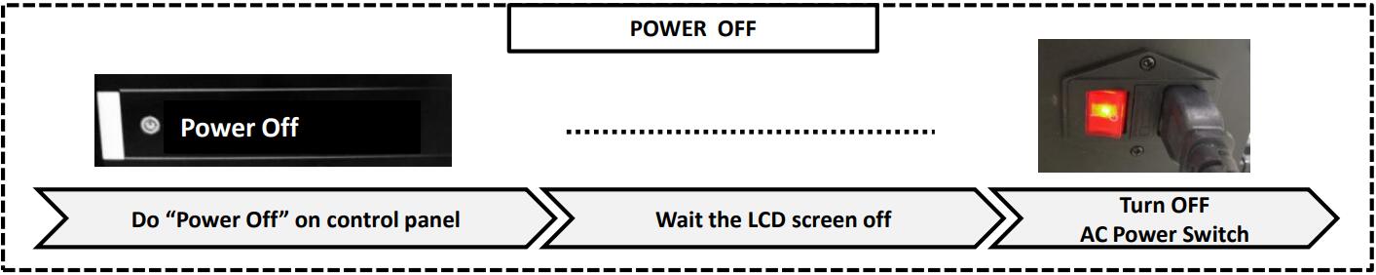
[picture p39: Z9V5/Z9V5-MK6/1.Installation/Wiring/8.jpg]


## Final inspection 
Now you have completed the wiring, but please follow the steps below to perform a simple inspection before using the machine.
1. Power on the printer.
2. Rotate and press the knob on the control panel (LCD screen) to check if the control panel is working properly.
3. Use the knob to move the menu "Prepare>>Auto Home>>Home All", and press the knob to do. The machine will follow these steps to operate:
    - The printing platform move down a few millimeters.
    - The Y-axis move forward until it reaches the Y ENDSTOP (a limit switch on the top-right of the machine).
    - The print head move to the left until the housing of the print head touches the X ENDSTOP (a limit switch on the top-left of the machine).
    - The printing platform move upwards until the Z-axis height adjustment screws touches the Z ENDSTOP (limit switch on the top of Z carrier).        
:warning: If the machine doesn't work properly, please refer to the [**:book:Troubleshooting Online Document**](https://github.com/ZONESTAR3D/Z9/tree/main/Z9V5/Z9V5_FAQ#faq-for-z9v5) to check it first.
4. Use the knob to move the menu "Prepare>>Temperature>>Preheat PLA", and press the knob to do. And then watch the hot bed and hot end temperature shows on LCD screen, they will rise up to the setting temperature.
5. Power off the printer after finish the above steps.
- **[:book:LCD Menu description Online Document](https://github.com/ZONESTAR3D/Z9/tree/main/Z9V5/Z9V5-MK6/2.Operation/LCDMENU_Description.md)**.
- **[:blue_book:LCD Menu description pdf file](./2.Operation/LCDMENU_Description.pdf)**.

----
## :fireworks: Congratulate! 
Now, you have completed the wiring. Next, please refer to the Operation manual to make necessary adjustments to the machine and complete several printing tests to familiarize yourself with the operation of the machine.
- **[:book:Operation Manual Online Document](https://github.com/ZONESTAR3D/Z9/tree/main/Z9V5/Z9V5-MK6/2.Operation/Operation.md)**.
- **[:blue_book:Operation Manual pdf file](./2.Operation/Operation.pdf)**.

----
### :page_facing_up: Appendix: Hotend cable
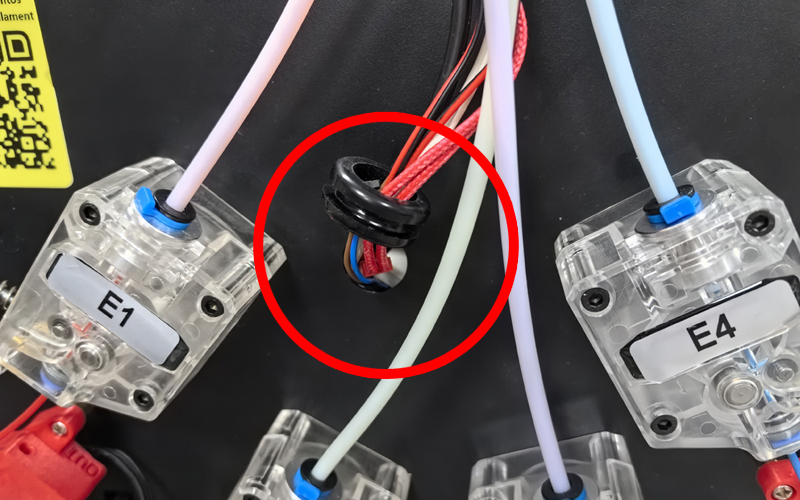
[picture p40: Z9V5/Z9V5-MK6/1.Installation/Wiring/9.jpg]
######  
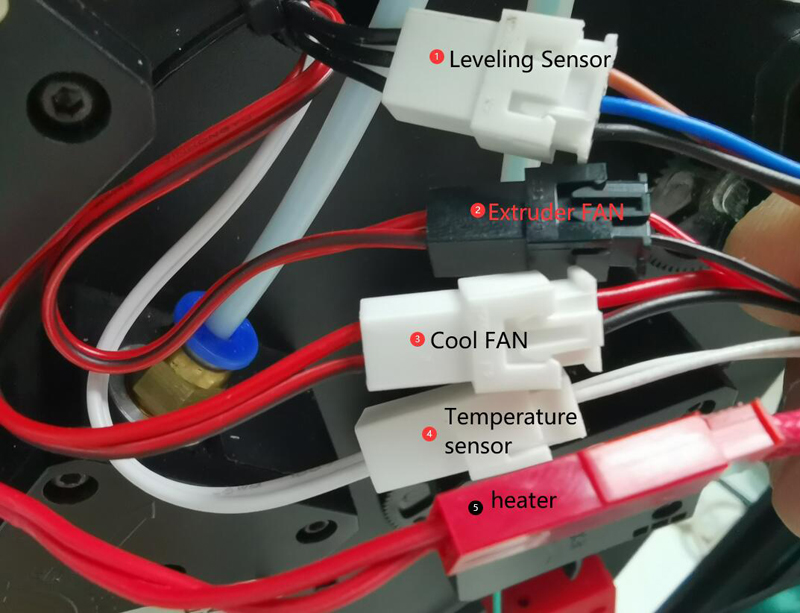
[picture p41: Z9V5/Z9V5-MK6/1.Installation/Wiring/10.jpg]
######

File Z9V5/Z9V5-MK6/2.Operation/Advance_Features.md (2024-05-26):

## Advance features
### Contents
- [**Bed auto leveling Feature**](#a1)
- [**Power Auto Shutdown Feature**](#a2)
- [**Auto Mixing Feature**](#a3)
- [**Filament Run Out Detect Feature**](#a4)
- [**Power Loss Recovery Feature**](#a5)
- [**Auto retract**](#a6)

----
### <a id="a1">Bed Auto Leveling</a>
#### [:clapper: Video tutorial](https://youtu.be/Zoyl6PybsUk)  
:book: Most beds appear quite flat and even, but even when the bed is flat, there may be irregularities due to tape or other matter on the surface. Bed Automatic Leveling helps improve the quality of printing and bed adhesion by taking several measurements of the bed surface and then adjusting all movement to follow the tilt or contours of the bed.   
#### Steps of turn on bed auto leveling feature:
##### :loudspeaker: If you have not done the auto leveling test before, or you have executed restore defaults, or you have upgraded the firmware, or the auto leveling data is incorrect. You need to redo these steps.   
1. Turn on Automatic Bed Leveling on LCD MENU ***Control>>Configre>>Auto Leveling***  
2. Do ***Prepare>>Bed Leveling>>Point 1 ~ Point 4*** and adjust the bed mounted screws to level the bed first.   
:loudspeaker: Wait for the hotbed and hotend to cool down if they were not cold before doing this step.  
:loudspeaker: Clean the nozzle, ensure there isn't any filament left on the nozzle.
3. Do ***Prepare>>Bed Leveling>>Catch Z offset***.
4. Do ***Prepare>>Bed Leveling>>Auto Lebeling***. After finished, you will get a "height error table" as below picture.
    - If the measured values are evenly distributed around 0, and the difference between the maximum value and the minimum value is less than 0.4 (***as shown in Figure 1***), we suggest that you do not need to enable the automatic leveling function.   
    - If most of the measured values are bigger than zero and the average value > 0.2 (***as shown in Figure 2***), please add the ***Preobe Z offset*** (new value = previous value + average value of measured (>0)  ) and do this steps again.
    - If most of the measured values are bigger than zero and the average value < -0.2 (***as shown in Figure 3***), please reduce the ***Preobe Z offset*** (new value = previous value + average value of measured (<0>)) and do this steps again.      
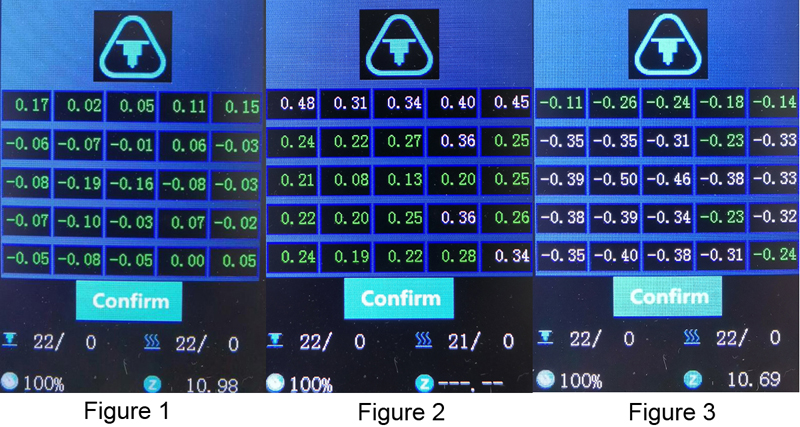
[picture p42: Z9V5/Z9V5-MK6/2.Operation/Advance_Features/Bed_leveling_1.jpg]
     
5. After completing the above steps, the automatic leveling function will be enabled, and then you can start printing the gcode file from SD card. However, when print the first the gcode file, it is possible that the nozzle may be slightly away from the hot bed, you need to double-click the knob to slightly adjust the height between the nozzle and the hot bed, about the steps, please refer to [:point_right: ***the step 4 of "Print your "Hellow World" works"***](https://github.com/ZONESTAR3D/Z9/blob/main/Z9V5/Z9V5-MK6/2.Operation/Operation.md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).
6. If you turn off the power of the machine and restart it, you need to turn on the bed automatic leveling function manually, that is, set the value of ***"Control>>Configre>>Active autolevel:"*** to ON in the LCD menu.    
:pushpin: For a more detailed user manual about bed automatic leveling, please refer to:
https://github.com/ZONESTAR3D/Upgrade-kit-guide/blob/main/Bed_Leveling_Sensor/PL-08N/ABL_LCDDWIN.md

----
### <a id="a2">Power auto shutdown</a>
#### [:clapper:Video tutorial](https://youtu.be/SJLpmJL-tG4).
#### Turn on the auto shutdown feature on LCD screen 
You can turn on the auto shut down feature on LCD sceen, after turned on it, the machine will shut down automatically:
1. In a non printing state, you did not perform any operations through the display knob within 15 minutes.
2. After the SD card printing is completed, the hot bed and hot end issues cool down to below the safe temperature for 15 minutes.      
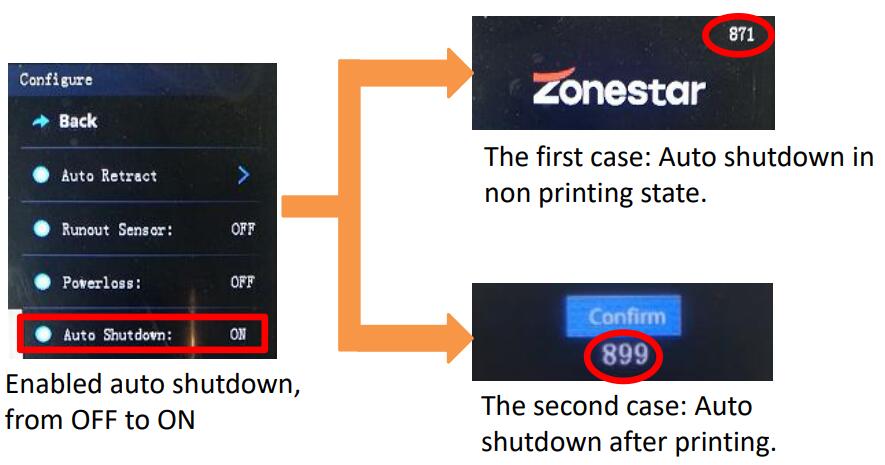
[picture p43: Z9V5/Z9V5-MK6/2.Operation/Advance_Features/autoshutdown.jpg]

#### Turn on the printer after print finish by adding command
You can also add a "M81" gcode command in the "End G-code" of the slicing software, it will turn off the printer after finished to print the gcode file.      
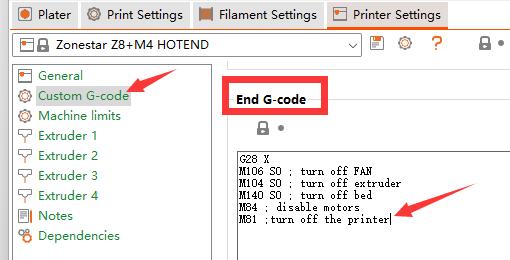
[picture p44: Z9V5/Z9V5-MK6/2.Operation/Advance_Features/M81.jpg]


----
### <a id="a3">Auto Mixing Feature</a>
The color mixing feature is a function to mix multi different color filaments and extruded from one nozzle to get a new color filament. By adjusting the extrude ratio of each extruder, it can get different color filament. For example, mix Magenta and Yellow filament as a ratio 5:1 to get Red filament, and mix Magenta and Yellow filament as a ratio 1:1 to get Orange filament, etc..    
For details about the Color Mixing Feature, please refer to https://github.com/ZONESTAR3D/Document-and-User-Guide/blob/master/Mixing_Color/Auto_Mixing.md.     
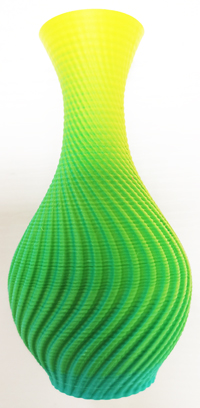
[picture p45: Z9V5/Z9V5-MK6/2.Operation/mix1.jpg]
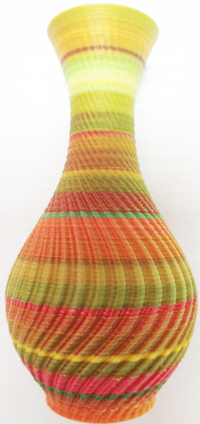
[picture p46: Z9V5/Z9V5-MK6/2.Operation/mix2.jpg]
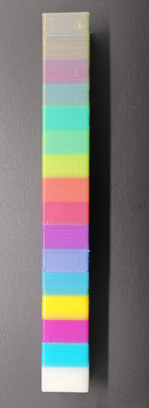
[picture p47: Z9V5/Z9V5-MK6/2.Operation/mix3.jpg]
   

----
### <a id="a4">Filament Run Out Detect</a>
#### Introduction of Filament Run Out Sensor
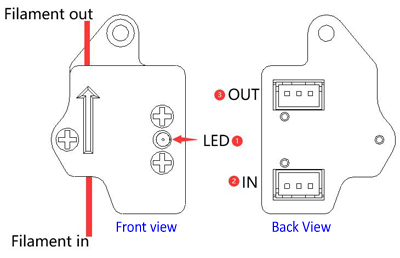
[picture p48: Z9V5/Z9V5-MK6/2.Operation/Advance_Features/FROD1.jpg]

- **LED:** Filament detection indicator light, it will light up when the filament is inserted.
- **"IN" Connector:** Connect to  the control board or the previous FROD.
- **"OUT" Connector:** Connect to the next FROD. Let it suspend if there is not the next one.   
:bulb:  The filament must be inserted in the direction indicated by the arrow.
#### Wiring diagram of Filament Run Out Sensors
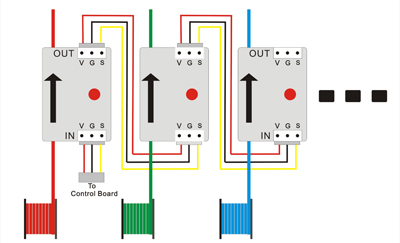
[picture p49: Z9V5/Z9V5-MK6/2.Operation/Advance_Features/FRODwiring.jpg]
    
:warning:The "Filament Run Out Sensors" (there are 4 pieces for Z9V5Pro) are series connected , it means any one "filament run out" is detected, the printer will pause printing.
#### [:clapper: Video tutorial](https://youtu.be/QCJ-6L6ze1w) 
If there is not enough filaments left in the filament roll to complete the current printing, you can enable the ***"Runout Sensor"*** feature. The machine will pause the printing when detected the filament is run out, then you can load a new filament roll and resume the printing. What you need to do is:    
1. Pass the filament through the **Filament Run Out Sensor**.
2. Turn on the **run out** feature on LCD screen.      
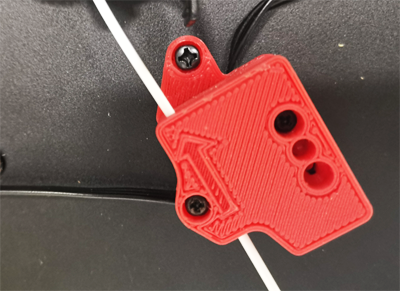
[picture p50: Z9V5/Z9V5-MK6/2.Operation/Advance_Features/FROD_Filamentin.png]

#### :warning: Notice
1. If you're sure that the filament is enough, do not pass the filament through the **Filament Run Out Sensor**.         
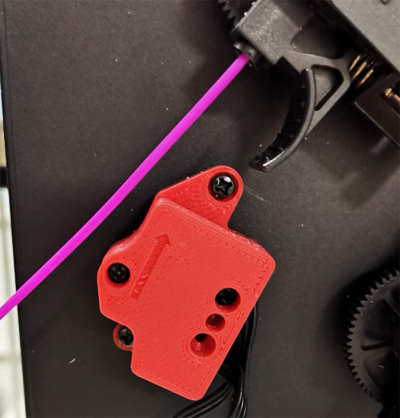
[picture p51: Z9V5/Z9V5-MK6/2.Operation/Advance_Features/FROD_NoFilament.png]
     
2. The printing pause may cause some obvious defects on the prints. 
3. If you need to use the Filament run out detect function, you should insert filaments on all 4 sensors. If you do not actually use 4 filaments when printing, you can cut a small segment of filaments and insert it into the shortage detection sensor. As shown in the following figure:     
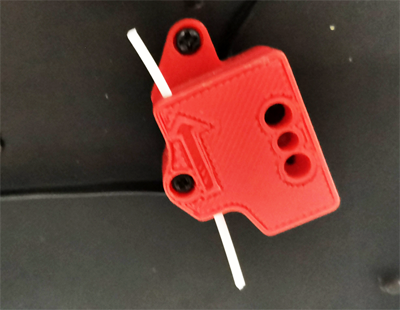
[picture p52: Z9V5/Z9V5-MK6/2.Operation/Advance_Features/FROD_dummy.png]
     

----
### <a id="a5">Power Loss Recovery</a>
#### [:clapper: **Video tutorial**](https://youtu.be/f-PpasByiiE)   
If your power supply network has frequent power outages, you can enable the automatic power losss recovery function before start printing. When the power goes out and it resumed, you can press the DC switch to turn on the power of the machine, and then the machine will automatically detect the printing breakpoint and provide you with whether you need to continue printing.    
#### :warning: Notice 
1. Breakpoints data and gcode files will be stored on the SD, must keep the SD card in socket before turn on the machine.       
2. The printing pause may cause some obvious defects on the prints.    

----
### <a id="a6">Auto retract</a>
The retraction setting is very effective in solving string issues. If you are not satisfied with the retraction parameters you set during slicing, you can enable "Auto Retract" function on the LCD menu. Once Auto Retract is enabled, the retraction parameters of the gcode file in the SD card will be replaced by the parameters in the LCD menu during the printing process, which will help you find the retraction settings suitable for your machine and filamanets.
### 1. Enter Auto Retract Menu Open the Configure Menu and click Auto Retract to enable 
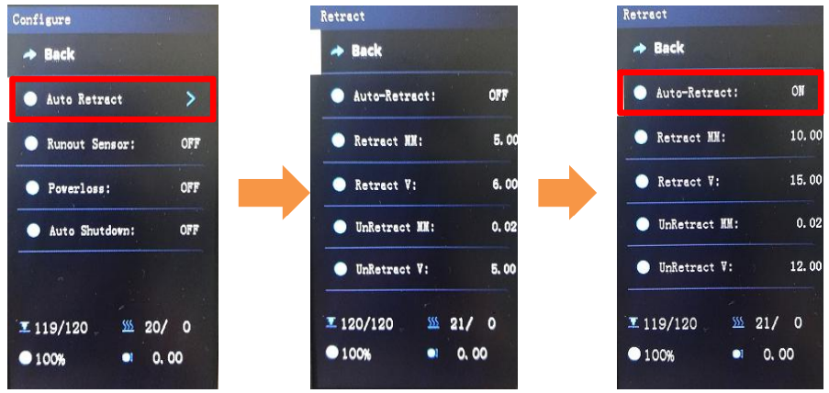
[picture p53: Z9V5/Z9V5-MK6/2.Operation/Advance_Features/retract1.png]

### 2. Setting parameters if need
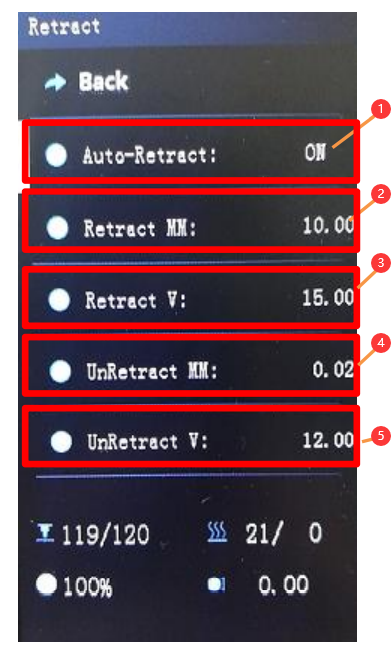
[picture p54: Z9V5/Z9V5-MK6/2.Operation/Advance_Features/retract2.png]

1. Turn ON / OFF auto retraction feature.      
2. Set retract distance (mm) for each extruder. 
3. Set retract speed (mm/s).
4. Set the overload filament length (mm) after each retraction.
5. Set reload speed (mm/s).

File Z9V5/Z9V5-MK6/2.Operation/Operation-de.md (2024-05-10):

## <a id="choose-language">:globe_with_meridians: Choose language </a>










----
## Bedienerführung
Bevor Sie mit dem Drucken beginnen, müssen Sie das heiße Bett nivellieren (den Abstand zwischen der Düse und der Druckplattform fein einstellen) und die Filamente in die Extruder und das heiße Ende laden.
## Das heiße Bett nivellieren
#### :warning: Bei einem FDM-3D-Drucker ist der Abstand zwischen der Düse und dem heißen Bett beim Drucken der ersten Schicht sehr wichtig. Ist der Abstand zu gering, können die Filamente nicht aus der Düse fließen und sogar die Düse und das heiße Bett beschädigen. Wenn der Abstand zu groß ist, können die Filamente nicht auf dem heißen Bett kleben, die nächsten Schichten können nicht richtig gestapelt werden und es kommt zu Druckfehlern.
###### (https://www.youtube.com/watch?v=jNf98S0u2VQ)
- **Schritt 1.** Schalten Sie den 3D-Drucker ein und führen Sie dann ***Prepare>>Auto Home>>Home All*** im LCD-MENÜ aus, warten Sie, bis das Hotend in die HOME-Position geht.
- **Schritt 2.** Ziehen Sie die Handmuttern unter dem Bett fest, um das Bett in die unterste Position zu bewegen (Abb. 1).
- **Schritt 3.** Führen Sie ***Prepare>> Bed leveling>> Point 1*** auf dem Bedienfeld aus (Abb. 2), die Düse geht zu den Ecken des Bettes, lösen Sie die Handmuttern unter dem Heizbett (Abb. 3) und lassen Sie die Düse fast das Brutbett berühren (Abb. 4). Fahren Sie mit ***Point 2/3/4*** fort, bis alle vier Ecken geebnet sind.
- **Schritt 4.** Wiederholen Sie Schritt 3 und machen Sie 2–3 Runden, bis alle vier Ecken auf der gleichen Höhe sind.
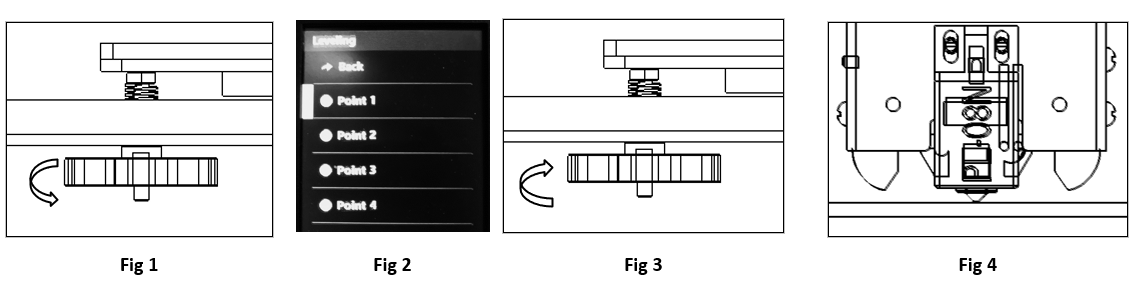
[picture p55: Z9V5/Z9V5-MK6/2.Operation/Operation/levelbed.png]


-----
### Filamente laden
###### (https://www.youtube.com/watch?v=1rr4dXRxKc4)
Dieser Drucker ist mit vier Extrudern und einem 4-IN-1-OUT-Farbmisch-Hot-End ausgestattet. Die Extruder und das Hot End sind durch eine Filamentführung (PTFE-Schlauch) verbunden. ***Vor dem Drucken müssen Sie alle 4 Filamente in die Extruder laden und sie unten in das heiße Ende einführen.***
- **Schritt 1.** Führen Sie auf dem Bedienfeld ***Prepare>>Auto Home>>Home All*** aus und führen Sie dann ***Prepare>>Temperature>> Preheat PLA*** aus. Wartende Düsentemperatur erreicht 190 ℃ (Abb. 1).
- **Schritt 2.** Schneiden Sie den Kopf des Filaments mit einer Diagonalzange ab (Abb. 2), drücken Sie dann auf den Griff des Extruders Nr. 1 und führen Sie das Filament ein. Drücken Sie das Filament, bis Sie das Filament im PTFE sehen können Anleitung (Abb. 3). Drehen Sie das Zahnrad von Extruder Nr. 1 (Abb. 4) und beobachten Sie das Filament, bis es unten in das heiße Ende gelangt.
- **Schritt 3.** Verwenden Sie die gleiche Methode wie in Schritt 2, um die Filamente in Extruder Nr. 2 bis Extruder Nr. 4 zu laden, und beobachten Sie die Filamente, bis sie die Unterseite des heißen Endes erreichen.
- **Schritt 4.** Drehen Sie langsam das Zahnrad von Extruder Nr. 1 bis Extruder Nr. 4 nacheinander und beobachten Sie die Düse, bis Sie sehen können, wie das Filament aus der Düse herausfließt (Abb. 5).
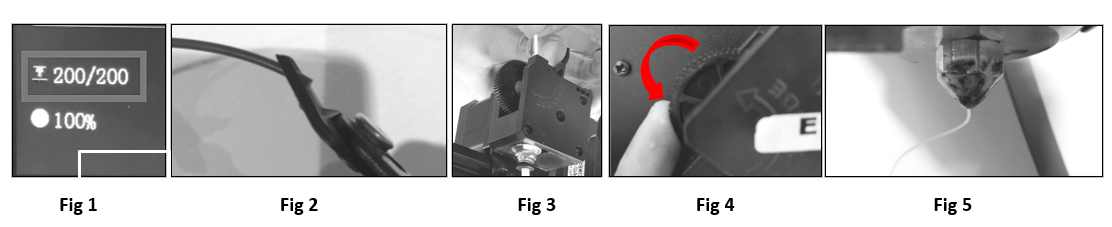
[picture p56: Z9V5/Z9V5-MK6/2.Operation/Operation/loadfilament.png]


-----
### Drucken Sie Ihre „Hellow World“-Werke aus
#### Drucken Sie eine einzelne Farbtestdatei
###### (https://www.youtube.com/watch?v=NbVy8NjKt_s)
- **Schritt 1.** Stecken Sie die SD-Karte in den SD-Kartensteckplatz am Drucker (Abb. 1).
- **Schritt 2.** Klicken Sie auf dem Bedienfeld auf das Symbol ***Print*** und wählen Sie ***xyz_cube.gcode*** (Abb. 2). Klicken Sie auf den Knopf, um mit dem Drucken zu beginnen.
- **Schritt 3.** Warten Sie, bis das Hotend und das Hotbed die eingestellte Temperatur erreicht haben (Abb. 3), die Düse kehrt zur Ursprungsposition zurück und bewegt sich dann über die Druckplattform und extrudiert das Filament mithilfe einer Pinzette um den Ausflussfaden zu entfernen (Abb. 4).
- **Schritt 4.** Wenn sich die Düse zum heißen Bett bewegt und mit dem Drucken beginnt, doppelklicken Sie auf den Knopf, um das Menü ***Babystep Z*** zu öffnen (Abb. 5). Drehen Sie den Knopf langsam, um die Höhe der Druckplattform fein einzustellen Beobachten Sie den Abstand von der Düse zum Bett, bis der Abstand gut passt (Abb. 6).
- **Schritt 5.** Warten Sie, bis der Druckvorgang abgeschlossen ist (Abb. 7), warten Sie, bis das Heizbett abgekühlt ist (Abb. 8), und entfernen Sie dann das gedruckte Objekt vom Heizbett (Abb. 9).
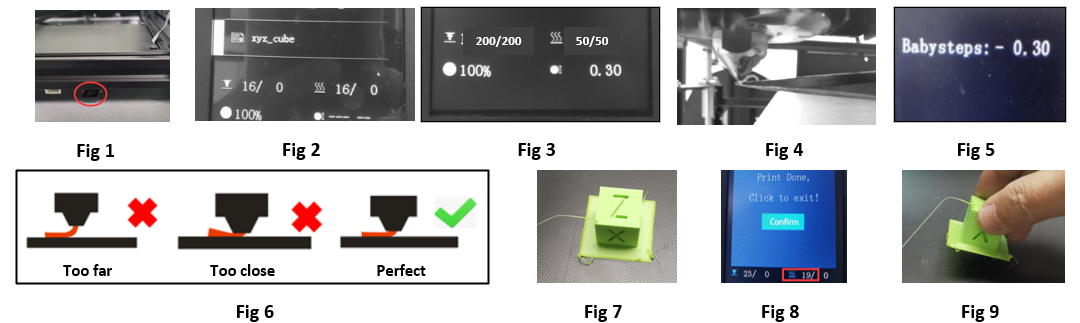
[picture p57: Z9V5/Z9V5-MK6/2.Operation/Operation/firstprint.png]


#### Drucken Sie eine mehrfarbige Testdatei
###### (https://www.youtube.com/watch?v=iddKadfrdjw)
Die Schritte für den Mehrfarbendruck und den Einzelfarbendruck sind grundsätzlich gleich, aber bevor Sie mit dem Drucken beginnen, extrudieren Sie bitte einige Filamente aus allen Extrudern, um sicherzustellen, dass das heiße Ende normal funktioniert.
- **Schritt 1.** Stecken Sie die SD-Karte in den SD-Kartensteckplatz am Drucker.
- **Schritt 2.** Erhitzen Sie die Düse und extrudieren Sie etwas Filament. **Prepare>>Filament: *Preheat Nozzle: 200* -> *Extruder: All* -> *Load Slowly***.
- **Schritt 3.** Klicken Sie auf dem Bedienfeld auf das Symbol „Drucken“ und wählen Sie ***M4_4CTest.gcode***. Klicken Sie auf den Knopf, um mit dem Drucken zu beginnen.
- **Schritt 4.** Passen Sie den Abstand von der Düse zum Bett fein an.
- **Schritt 5.** Warten Sie, bis der Druckvorgang abgeschlossen ist

-----
### :fireworks: Herzlichen Glückwunsch!
Nachdem Sie die ersten Werke gedruckt haben, haben Sie ein grundlegendes Verständnis für die Funktionsweise des 3D-Druckers. Anschließend können Sie weitere Testdateien ausdrucken oder Ihr eigenes 3D-Modell in Scheiben schneiden und mit dem Gerät ausdrucken.
Es wird empfohlen, die Slicing-Software herunterzuladen und zu installieren und das Benutzerhandbuch der Slicing-Software zu lesen, um zu erfahren, wie man sie verwendet. Einzelheiten finden Sie im [:book: **Schnittanleitung**](https://github.com/ZONESTAR3D/Z9/tree/main/Z9V5/Z9V5-MK6/4.Slicing).

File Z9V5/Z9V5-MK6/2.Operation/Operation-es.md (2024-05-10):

## <a id="choose-language">:globe_with_meridians: Choose language </a>










----
## Manual de operaciones
Antes de comenzar a imprimir, debe nivelar la cama caliente (ajustar la distancia entre la boquilla y la plataforma de impresión) y cargar los filamentos en las extrusoras y el extremo caliente.
## Nivelar la cama caliente
#### :warning: Para impresoras 3D FDM, la distancia entre la boquilla y la cama caliente es muy importante al imprimir la primera capa. Si la distancia es demasiado corta, los filamentos no pueden salir de la boquilla e incluso dañan la boquilla y la cama caliente. Si la distancia es demasiado grande, los filamentos no se pueden pegar en la cama caliente, las siguientes capas no se pueden apilar correctamente y provocan errores de impresión.
###### (https://www.youtube.com/watch?v=jNf98S0u2VQ)
- **Paso 1.** Encienda la impresora 3D y luego haga ***Preparar>>Inicio automático>>Inicio todo*** en el MENÚ LCD, espere que el hotend vaya a la posición INICIO.
- **Paso 2.** Apriete las tuercas manuales debajo de la cama para bajar la cama a la posición más baja (Fig. 1).
- **Paso 3.** Haga ***Preparar>> Nivelación de la cama>> Punto 1*** en el panel de control (Fig. 2), la boquilla irá a las esquinas de la cama, afloje las tuercas manuales debajo de la cama caliente. (Fig. 3) y deje que la boquilla casi toque el foco (Fig. 4). Continúe haciendo el ***Punto 2/3/4*** hasta que se hayan nivelado las 4 esquinas.
- **Paso 4.** Repita el paso 3 y haga 2 ~ 3 rondas, hasta que las cuatro esquinas estén a la misma altura.


----
### Cargar filamentos
###### (https://www.youtube.com/watch?v=1rr4dXRxKc4)
Esta impresora está equipada con cuatro extrusoras y un extremo caliente de mezcla de colores 4 EN 1 SALIDA. Los extrusores y el hot end están conectados mediante una guía de filamento (tubo de PTFE). ***Antes de imprimir, debes cargar los 4 filamentos en los extrusores e introducirlos en la parte inferior del extremo caliente.***
- **Paso 1.** Haga ***Preparar>>Inicio automático>>Inicio todo*** en el panel de control, y luego haga ***Preparar>>Temperatura>> Precalentar PLA***, esperando que se alcance la temperatura de la boquilla. a 190 ℃ (Figura 1).
- **Paso 2.** Utilice unos alicates diagonales para cortar la cabeza del filamento (Fig. 2), y luego presione el mango del extrusor n.º 1 e inserte el filamento, empuje el filamento hasta que pueda ver el filamento en el PTFE. guía (Figura 3). Gire el engranaje del extrusor n.º 1 (Fig. 4), observe el filamento hasta que entre en la parte inferior del extremo caliente.
- **Paso 3.** Usando el mismo método que en el paso 2 para cargar los filamentos en el extrusor n.° 2 ~ extrusor n.° 4, observe los filamentos hasta que entren en la parte inferior del extremo caliente.
- **Paso 4.** Gire lentamente los engranajes del extrusor n.° 1 ~ extrusor n.° 4 uno por uno y observe la boquilla, hasta que pueda ver que el filamento sale de la boquilla (Fig. 5).


----
### Imprime tus obras de "Hellow World"
#### Imprimir un archivo de prueba de un solo color
###### (https://www.youtube.com/watch?v=NbVy8NjKt_s)
- **Paso 1.** Inserte la tarjeta SD en el zócalo para tarjetas SD de la impresora (Fig. 1).
- **Paso 2.** Haga clic en el ICONO ***Imprimir*** en el panel de control y elija ***xyz_cube.gcode*** (Fig. 2), haga clic en la perilla para comenzar a imprimir.
- **Paso 3.** Espere hasta que el hotend y el hotend alcancen la temperatura establecida (Fig. 3), la boquilla regresará a la posición de origen y luego se moverá hacia arriba de la plataforma de impresión y extruirá el filamento, use unas pinzas. para retirar el filamento de salida (Fig. 4).
- **Paso 4.** Cuando la boquilla se movió a la cama caliente y comenzó a imprimir, haga doble clic en la perilla para abrir un menú **Babystep Z** (Fig. 5), gire la perilla lentamente para ajustar la altura de impresión. plataforma, observar la distancia desde la boquilla hasta la cama, hasta que la distancia sea buena (Fig. 6).
- **Paso 5.** Espere a que finalice la impresión (Fig. 7), espere a que se enfríe la base (Fig. 8) y luego retire el objeto impreso de la base (Fig. 9).


#### Imprimir un archivo de prueba multicolor
###### (https://www.youtube.com/watch?v=iddKadfrdjw)
Los pasos para la impresión multicolor y la impresión de un solo color son básicamente los mismos, pero antes de comenzar a imprimir, extruya algunos filamentos de todas las extrusoras para confirmar que el extremo caliente funciona normalmente.
- **Paso 1.** Inserte la tarjeta SD en el zócalo para tarjetas SD de la impresora.
- **Paso 2.** Calentar la boquilla y extruir un poco de filamento. **Preparar>>Filamento: *Precalentar boquilla: 200* -> *Extrusora: Todo* -> *Cargar lentamente***.
- **Paso 3.** Haga clic en el ICONO "Imprimir" en el panel de control y elija ***M4_4CTest.gcode***, haga clic en la perilla para comenzar a imprimir.
- **Paso 4.** Ajuste con precisión la distancia entre la boquilla y la cama.
- **Paso 5.** Espere a que finalice la impresión.

----
### :fireworks: ¡Felicitaciones!
Después de imprimir los primeros trabajos, tendrá una comprensión básica de cómo funciona la impresora 3D. A continuación, puede imprimir otros archivos de prueba o cortar su propio modelo 3D y utilizar la máquina para imprimirlo.
Se recomienda descargar e instalar el software de corte y leer la guía del usuario del software de corte para saber cómo usarlo. Para obtener más detalles, consulte el [:book: **Guía de corte**](https://github.com/ZONESTAR3D/Z9/tree/main/Z9V5/Z9V5-MK6/4.Slicing).

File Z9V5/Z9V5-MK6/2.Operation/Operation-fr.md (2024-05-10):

## <a id="choose-language">:globe_with_meridians: Choose language </a>










----
## Guide d'opération
Avant de commencer l'impression, vous devez niveler le lit chaud (ajuster finement la distance entre la buse et la plate-forme d'impression) et charger les filaments dans les extrudeuses et la partie chaude.
## Mise à niveau du lit chaud
#### :warning: Pour une imprimante 3D FDM, la distance entre la buse et le lit chaud est très importante lors de l'impression de la première couche. Si la distance est trop proche, les filaments ne peuvent pas s'écouler hors de la buse, et même endommager la buse et le lit chaud. Si la distance est trop grande, les filaments ne peuvent pas être collés sur le lit chaud, les couches suivantes ne peuvent pas être empilées correctement et entraîner un échec d'impression.
###### (https://www.youtube.com/watch?v=jNf98S0u2VQ)
- **Étape 1.** Allumez l'imprimante 3D, puis faites ***Prepare>>Auto Home>>Home All*** sur le MENU LCD, attendez que le hotend aille en position HOME.
- **Étape 2.** Serrez les écrous manuels sous le lit pour faire descendre le lit jusqu'à la position la plus basse (Fig. 1).
- **Étape 3.** Faites ***Préparer>> Nivellement du lit>> Point 1*** sur le panneau de commande (Fig 2), la buse ira jusqu'aux coins du lit, desserrez les écrous à main sous le foyer (Fig. 3) et laissez la buse toucher presque le foyer (Fig. 4). Continuez à faire le ***Point 2/3/4*** jusqu'à ce que les 4 coins soient nivelés.
- **Étape 4.** Répétez l'étape 3 et faites 2 à 3 tours, jusqu'à ce que les quatre coins soient à la même hauteur.


----
### Charger les filaments
###### (https://www.youtube.com/watch?v=1rr4dXRxKc4)
Cette imprimante est équipée de quatre extrudeuses et d'une extrémité chaude de mélange de couleurs 4-IN-1-OUT. Les extrudeuses et le hot end sont reliés par un guide filament (tube PTFE). ***Avant d'imprimer, vous devez charger les 4 filaments dans les extrudeuses et les insérer dans le bas de l'extrémité chaude.***
- **Étape 1.** Faites ***Préparation>>Auto Accueil>>Maison Tout*** sur le panneau de commande, puis faites ***Préparation>>Température>> Préchauffer le PLA***, en attendant que la température de la buse soit atteinte. à 190 ℃ (Fig. 1).
- **Étape 2.** Utilisez une pince diagonale pour couper la tête du filament (Fig. 2), puis appuyez sur la poignée de l'extrudeuse n°1 et insérez le filament, poussez le filament jusqu'à ce que vous puissiez voir le filament dans le PTFE. guide (Fig. 3). Faites tourner l'engrenage de l'extrudeuse n°1 (Fig. 4), observez le filament jusqu'à ce qu'il entre au bas de l'extrémité chaude.
- **Étape 3.** En utilisant la même méthode qu'à l'étape 2 pour charger les filaments dans l'extrudeuse n°2 ~ l'extrudeuse n°4, surveillez les filaments jusqu'à ce qu'ils entrent dans le bas de l'extrémité chaude.
- **Étape 4.** Faites tourner lentement l'engrenage de l'extrudeuse n°1 ~ de l'extrudeuse n°4 un par un et observez la buse jusqu'à ce que vous puissiez voir le filament s'écouler de la buse (Fig. 5).


----
### Imprimez vos travaux "Hellow World"
#### Imprimer un fichier de test d'une seule couleur
###### (https://www.youtube.com/watch?v=NbVy8NjKt_s)
- **Étape 1.** Insérez la carte SD dans la prise pour carte SD de l'imprimante (Fig 1).
- **Étape 2.** Cliquez sur l'ICÔNE ***Imprimer*** sur le panneau de commande et choisissez ***xyz_cube.gcode*** (Fig 2), cliquez sur le bouton pour lancer l'impression.
- **Étape 3.** Attendez que la hotend et le foyer atteignent la température de réglage (Fig. 3), la buse reviendra à la position d'origine, puis se déplacera au-dessus de la plate-forme d'impression et extrudera le filament, utilisez une pince à épiler. pour retirer le filament de sortie (Fig. 4).
- **Étape 4.** Lorsque la buse s'est déplacée vers le lit chaud et commence à imprimer, double-cliquez sur le bouton pour ouvrir un menu **Babystep Z** (Fig 5), tournez lentement le bouton pour affiner la hauteur d'impression. plate-forme, surveillez la distance entre la buse et le lit, jusqu'à ce que la distance soit bonne (Fig. 6).
- **Étape 5.** Attendez la fin de l'impression (Fig. 7), attendez que le foyer refroidisse (Fig. 8), puis retirez l'objet imprimé du foyer (Fig. 9).


#### Imprimer un fichier de test multicolore
###### (https://www.youtube.com/watch?v=iddKadfrdjw)
Les étapes pour l'impression multicolore et l'impression monochrome sont fondamentalement les mêmes, mais avant de commencer l'impression, veuillez extruder quelques filaments de toutes les extrudeuses pour confirmer que l'extrémité chaude fonctionne normalement.
- **Étape 1.** Insérez la carte SD dans la prise pour carte SD de l'imprimante.
- **Étape 2.** Chauffez la buse et extrudez du filament. **Préparer>>Filament : *Préchauffer la buse : 200* -> *Extrudeuse : Tout* -> *Charger lentement***.
- **Étape 3.** Cliquez sur l'ICÔNE « Imprimer » sur le panneau de commande et choisissez ***M4_4CTest.gcode***, cliquez sur le bouton pour lancer l'impression.
- **Étape 4.** Ajustez finement la distance entre la buse et le lit.
- **Étape 5.** Attendez que l'impression soit terminée.

-----
### :fireworks: Félicitations !
Après avoir imprimé les premières œuvres, vous avez une compréhension de base du fonctionnement de l’imprimante 3D. Ensuite, vous pouvez imprimer d'autres fichiers de test ou découper votre propre modèle 3D et utiliser la machine pour l'imprimer.
Il est recommandé de télécharger et d'installer le logiciel de découpage, et de lire le guide de l'utilisateur du logiciel de découpage pour savoir comment l'utiliser. Pour plus de détails, veuillez vous référer au [:book: **Guide de découpage**](https://github.com/ZONESTAR3D/Z9/tree/main/Z9V5/Z9V5-MK6/4.Slicing).

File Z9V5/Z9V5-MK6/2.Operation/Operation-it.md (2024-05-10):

## <a id="choose-language">:globe_with_meridians: Choose language </a>










----
## Guida operativa
Prima di iniziare a stampare, è necessario livellare il letto caldo (regolare con precisione la distanza tra l'ugello e la piattaforma di stampa) e caricare i filamenti negli estrusori e nell'estremità calda.
## Livellamento del letto caldo
#### :warning: per le stampanti 3D FDM, la distanza tra l'ugello e il letto caldo è molto importante quando si stampa il primo strato. Se la distanza è troppo ravvicinata, i filamenti non potranno fuoriuscire dall'ugello e potrebbero addirittura danneggiare l'ugello e il letto caldo. Se la distanza è eccessiva, i filamenti non possono incollarsi sul letto caldo, gli strati successivi non possono essere impilati correttamente e la stampa fallisce.
###### (https://www.youtube.com/watch?v=jNf98S0u2VQ)
- **Passaggio 1.** Accendi la stampante 3D e poi esegui ***Prepara>>Auto Home>>Home All*** sul MENU LCD, attendi che l'hotend raggiunga la posizione HOME.
- **Passaggio 2.** Stringere i dadi a mano sotto il letto per abbassare il letto nella posizione più bassa (Fig. 1).
- **Passaggio 3.** Eseguire ***Preparazione>> Livellamento del letto>> Punto 1*** sul pannello di controllo (Fig 2), l'ugello andrà agli angoli del letto, allentare i dadi a mano sotto il piano caldo (Fig 3) e lasciare che l'ugello quasi tocchi il piano caldo (Fig 4). Continua a fare ***Punto 2/3/4*** finché tutti e 4 gli angoli non saranno stati livellati.
- **Passaggio 4.** Ripeti il passaggio 3 ed esegui 2 ~ 3 giri, fino a quando tutti e quattro gli angoli sono alla stessa altezza.


----
### Caricare i filamenti
###### (https://www.youtube.com/watch?v=1rr4dXRxKc4)
Questa stampante è dotata di quattro estrusori e un hot end per la miscelazione dei colori 4-IN-1-OUT. Gli estrusori e l'hot end sono collegati da una guida del filamento (tubo in PTFE). ***Prima di stampare, è necessario caricare tutti e 4 i filamenti negli estrusori e inserirli nella parte inferiore dell'hot end.***
- **Passaggio 1.** Eseguire ***Preparazione>>Auto Home>>Home All*** sul pannello di controllo, quindi eseguire ***Preparazione>>Temperatura>> Preriscaldamento PLA***, in attesa che venga raggiunta la temperatura dell'ugello a 190 ℃ (Fig. 1).
- **Passaggio 2.** Utilizzare una pinza diagonale per tagliare la testa del filamento (Fig 2), quindi premere la maniglia dell'estrusore n. 1 e inserire il filamento, spingere il filamento finché non si vede il filamento nel PTFE guida (Fig. 3). Ruota l'ingranaggio dell'estrusore n. 1 (Fig. 4), osserva il filamento finché non entra nella parte inferiore dell'hot end.
- **Passaggio 3.** Utilizzando lo stesso metodo del passaggio 2 per caricare i filamenti nell'estrusore n. 2 ~ estrusore n. 4, osservare i filamenti finché non entrano nella parte inferiore dell'hot end.
- **Passaggio 4.** Ruota lentamente l'ingranaggio dell'estrusore n. 1 ~ dell'estrusore n. 4 uno alla volta e osserva l'ugello, finché non vedi il filamento fuoriuscire dall'ugello (Fig 5).


----
### Stampa i tuoi lavori "Hellow World".
#### Stampa un file di prova a colore singolo
###### (https://www.youtube.com/watch?v=NbVy8NjKt_s)
- **Passaggio 1.** Inserire la scheda SD nell'apposita presa sulla stampante (Fig. 1).
- **Passaggio 2.** Fare clic sull'ICONA ***Stampa*** sul pannello di controllo e scegliere ***xyz_cube.gcode*** (Fig 2), fare clic sulla manopola per avviare la stampa.
- **Passaggio 3.** Attendere fino a quando l'hotend e il piano caldo raggiungono la temperatura impostata (Fig 3), l'ugello si posizionerà nella posizione di origine, quindi si sposterà sopra la piattaforma di stampa ed estruderà il filamento, utilizzare una pinzetta per rimuovere il filamento in uscita (Fig 4).
- **Passaggio 4.** Quando l'ugello si è spostato sul letto caldo e ha iniziato a stampare, fare doppio clic sulla manopola per aprire il menu **Babystep Z** (Fig. 5), ruotare lentamente la manopola per regolare con precisione l'altezza di stampa piattaforma, osservare la distanza dall'ugello al letto, fino a quando la distanza non risulta ottimale (Fig. 6).
- **Passaggio 5.** Attendi che la stampa sia terminata (Fig 7), quindi attendi che il piano caldo si raffreddi (Fig 8), quindi rimuovi l'oggetto stampato dal piano caldo (Fig 9).


#### Stampa un file di prova a più colori
###### (https://www.youtube.com/watch?v=iddKadfrdjw)
I passaggi per la stampa multicolore e per la stampa a colore singolo sono sostanzialmente gli stessi, ma prima di iniziare la stampa, estrudere alcuni filamenti da tutti gli estrusori per verificare che l'hot end funzioni normalmente.
- **Passaggio 1.** Inserire la scheda SD nella presa per scheda SD sulla stampante.
- **Passaggio 2.** Riscalda l'ugello ed estrudi del filamento. **Prepara >>Filamento: *Preriscalda ugello: 200* -> *Estrusore: Tutto* -> *Carica lentamente***.
- **Passaggio 3.** Fai clic sull'ICONA "Stampa" sul pannello di controllo e scegli ***M4_4CTest.gcode***, fai clic sulla manopola per avviare la stampa.
- **Passaggio 4.** Regola con precisione la distanza dall'ugello al letto.
- **Passaggio 5.** Attendi il completamento della stampa.

-----
### :fireworks: Congratulazioni!
Dopo aver stampato i primi lavori, hai una conoscenza di base di come funziona la stampante 3d. Successivamente, puoi stampare altri file di prova o tagliare il tuo modello 3D e utilizzare la macchina per stamparlo.
Si consiglia di scaricare e installare il software di slicing e di leggere la guida utente del software di slicing per sapere come utilizzarlo. Per i dettagli, fare riferimento al [:book: **Guida allo slicing**](https://github.com/ZONESTAR3D/Z9/tree/main/Z9V5/Z9V5-MK6/4.Slicing).

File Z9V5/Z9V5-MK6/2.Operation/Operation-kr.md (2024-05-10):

## <a id="choose-language">:globe_with_meridians: Choose language </a>










----
## 운영안내
프린팅을 시작하기 전에 핫베드의 수평을 맞추고(노즐과 프린팅 플랫폼 사이의 거리를 미세 조정) 필라멘트를 압출기와 핫엔드에 로드해야 합니다.
## 핫베드 수평 맞추기
#### :warning: FDM 3D 프린터의 경우 첫 번째 레이어를 인쇄할 때 노즐과 핫베드 사이의 거리가 매우 중요합니다. 거리가 너무 가까우면 노즐 밖으로 필라멘트가 흘러나오지 못하고, 심지어 노즐과 핫베드가 손상될 수 있습니다. 거리가 너무 멀면 필라멘트가 핫베드에 붙지 못하고 다음 레이어가 제대로 쌓이지 않아 프린팅이 실패할 수 있습니다.
###### (https://www.youtube.com/watch?v=jNf98S0u2VQ)
- **1단계.** 3D 프린터의 전원을 켜고 LCD 메뉴에서 ***Prepare>>Auto Home>>Home All*** 을 수행하고 핫엔드가 홈 위치로 이동하기를 기다립니다.
- **2단계.** 침대 아래 핸드 너트를 조여 침대를 가장 낮은 위치로 이동합니다(Fig 1).
- **3단계.** ***Prepare>> Bed leveling>> Point 1*** 지점(Fig 2)을 수행하면 노즐이 베드 모서리로 이동하고 온상 아래의 핸드 너트를 푼다. (Fig 3) 그리고 노즐이 온상에 거의 닿도록 합니다(Fig 4). 4개의 모서리가 모두 수평이 될 때까지 ***Point 2/3/4***을 계속 수행하세요.
- **4단계.** 네 모서리가 모두 같은 높이가 될 때까지 3단계를 반복하고 2~3회 반복합니다.


----
### 필라멘트 로드
###### (https://www.youtube.com/watch?v=1rr4dXRxKc4)
이 프린터에는 4개의 압출기와 1개의 4-IN-1-OUT 색상 혼합 핫엔드가 장착되어 있습니다. 압출기와 핫 엔드는 필라멘트 가이드(PTFE 튜브)로 연결됩니다. ***프린팅하기 전에 필라멘트 4개를 모두 압출기에 로드하고 핫엔드 바닥에 공급해야 합니다.***
- **1단계.** 제어판에서 ***Prepare>>Auto Home>>Home All*** 을 수행한 다음 ***Prepare>>Temperature>> Preheat PLA*** 을 수행하고 노즐 온도 도달 대기 190℃까지(Fig 1).
- **Step 2.** 대각선 펜치를 사용하여 필라멘트 헤드를 잘라낸 후(Fig 2), Extruder#1의 손잡이를 누르고 필라멘트를 삽입한 후 PTFE에 필라멘트가 보일 때까지 밀어 넣습니다. 가이드(Fig 3). 압출기 #1(Fig 4)의 기어를 회전하고 필라멘트가 핫 엔드 바닥에 들어갈 때까지 지켜봅니다.
- **Step 3.** 2단계와 동일한 방법으로 필라멘트를 Extruder#2 ~ Extruder#4에 로딩하여 필라멘트가 핫엔드 하단으로 들어갈 때까지 지켜봅니다.
- **Step 4.** Extruder#1 ~ Extruder#4의 기어를 하나씩 천천히 돌리면서 필라멘트가 노즐에서 흘러나오는 것을 볼 수 있을 때까지 노즐을 관찰합니다(Fig 5).


----
### "Hello World"" 작품을 인쇄하세요.
#### 단일 색상 테스트 파일 인쇄
###### (https://www.youtube.com/watch?v=NbVy8NjKt_s)
- **1단계.** SD 카드를 프린터의 SD 카드 소켓에 삽입합니다(Fig 1).
- **2단계.** 제어판에서 ***Print*** 아이콘을 클릭하고 ***xyz_cube.gcode***(Fig 2)를 선택한 다음 손잡이를 클릭하여 인쇄를 시작합니다.
- **3단계.** 핫엔드와 핫베드가 설정 온도에 도달할 때까지 기다리면(Fig 3), 노즐이 원점 위치로 이동한 다음 프린팅 플랫폼 위로 이동하여 필라멘트를 압출하고 핀셋을 사용합니다. 유출 필라멘트를 제거합니다(Fig 4).
- **Step 4.** 노즐이 핫베드로 이동하고 인쇄가 시작되면 손잡이를 두 번 클릭하여 **Babystep Z** 메뉴(Fig 5)를 열고 손잡이를 천천히 돌려 인쇄 높이를 미세 조정합니다. 플랫폼에서 거리가 잘 나올 때까지 노즐에서 베드까지의 거리를 관찰합니다(Fig 6).
- **5단계.** 프린팅이 완료되기를 기다리고(Fig 7), 핫베드가 식을 때까지 기다린 후(Fig 8), 프린팅된 대상물을 핫베드에서 꺼냅니다(Fig 9).


#### 멀티 컬러 테스트 파일 인쇄
###### (https://www.youtube.com/watch?v=iddKadfrdjw)
다색 인쇄 및 단색 인쇄 단계는 기본적으로 동일하지만 인쇄를 시작하기 전에 모든 압출기에서 일부 필라멘트를 압출하여 핫 엔드가 정상적으로 작동하는지 확인하십시오.
- **1단계.** SD 카드를 프린터의 SD 카드 소켓에 삽입합니다.
- **2단계.** 노즐을 가열하고 필라멘트를 압출합니다. **Prepare>>Filament: *Preheat Nozzle: 200* -> *Extruder: All* -> *Load Slowly***.
- **3단계.** 제어판에서 "인쇄" 아이콘을 클릭하고 ***M4_4CTest.gcode***를 선택한 후 손잡이를 클릭하여 인쇄를 시작합니다.
- **4단계.** 노즐에서 베드까지의 거리를 미세 조정합니다.
- **5단계.** 인쇄가 완료될 때까지 기다립니다.

-----
### :fireworks: 축하합니다!
첫 번째 작품을 프린트한 후에는 3D 프린터의 작동 방식에 대한 기본적인 이해를 갖게 됩니다. 다음으로, 다른 테스트 파일을 인쇄하거나 자신의 3D 모델을 슬라이스하고 기계를 사용하여 인쇄할 수 있습니다.
슬라이싱 소프트웨어를 다운로드하여 설치하는 것이 좋으며, 슬라이싱 소프트웨어의 사용자 가이드를 읽어 사용법을 숙지하시기 바랍니다. 자세한 내용은 [:book: **슬라이싱 가이드**](https://github.com/ZONESTAR3D/Z9/tree/main/Z9V5/Z9V5-MK6/4.Slicing).

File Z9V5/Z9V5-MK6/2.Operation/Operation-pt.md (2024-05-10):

## <a id="choose-language">:globe_with_meridians: Choose language </a>










----
## Guia de operação
Antes de iniciar a impressão, é necessário nivelar a cama quente (ajustar a distância entre o bico e a plataforma de impressão) e carregar os filamentos nas extrusoras e na extremidade quente.
## Nivelando a cama quente
#### :warning: Para impressoras 3D FDM, a distância entre o bico e a cama quente é muito importante ao imprimir a primeira camada. Se a distância for muito próxima, os filamentos não podem fluir para fora do bico e até danificar o bico e a cama quente. Se a distância for muito grande, os filamentos não poderão ser colados na cama quente, as próximas camadas não poderão ser empilhadas corretamente e causarão falha na impressão.
###### (https://www.youtube.com/watch?v=jNf98S0u2VQ)
- **Etapa 1.** Ligue a impressora 3D e então faça ***Prepare>>Auto Home>>Home All*** no LCD MENU, espere o hotend ir para a posição HOME.
- **Etapa 2.** Aperte as porcas manuais sob a cama para descer a cama até a posição mais baixa (Fig 1).
- **Etapa 3.** Faça ***Preparar>> Nivelamento da cama>> Ponto 1*** no painel de controle (Fig 2), o bico irá para os cantos da cama, afrouxe as porcas manuais sob o viveiro (Fig 3) e deixe o bico quase tocar no viveiro (Fig 4). Continue fazendo ***Ponto 2/3/4*** até que todos os 4 cantos estejam nivelados.
- **Etapa 4.** Repita a Etapa 3 e faça 2 a 3 voltas, até que todos os quatro cantos estejam na mesma altura.


----
### Carregar filamentos
###### (https://www.youtube.com/watch?v=1rr4dXRxKc4)
Esta impressora está equipada com quatro extrusoras e um hot end de mistura de cores 4-IN-1-OUT. As extrusoras e o hot end são conectados por uma guia de filamento (tubo de PTFE). ***Antes de imprimir, você precisa carregar todos os 4 filamentos nas extrusoras e alimentá-los na parte inferior da extremidade quente.***
- **Etapa 1.** Faça ***Prepare>>Auto Home>>Home All*** no painel de controle e, em seguida, faça ***Prepare>>Temperature>> Preheat PLA***, aguardando que a temperatura do bico seja atingida a 190 ℃ (Fig. 1).
- **Etapa 2.** Use um alicate diagonal para cortar a cabeça do filamento (Fig 2) e, em seguida, pressione a alça da extrusora nº 1 e insira o filamento, empurre o filamento até poder ver o filamento no PTFE guia (Fig. 3). Gire a engrenagem da extrusora nº 1 (Fig 4), observe o filamento até que ele entre na parte inferior do hot end.
- **Etapa 3.** Usando o mesmo método da etapa 2 para carregar os filamentos na extrusora#2 ~ extrusora#4, observe os filamentos até que eles entrem na parte inferior da extremidade quente.
- **Etapa 4.** Gire lentamente a engrenagem da extrusora#1 ~ extrusora#4 uma por uma e observe o bico, até que você possa ver o filamento fluindo para fora do bico (Fig 5).


----
### Imprima seus trabalhos do "Hellow World""
#### Imprimir um arquivo de teste de cor única
###### (https://www.youtube.com/watch?v=NbVy8NjKt_s)
- **Etapa 1.** Insira o cartão SD no slot de cartão SD da impressora (Fig 1).
- **Etapa 2.** Clique no ÍCONE ***Imprimir*** no painel de controle e escolha ***xyz_cube.gcode*** (Fig 2), clique no botão para iniciar a impressão.
- **Etapa 3.** Espere até que o hotend e o hotbed atinjam a temperatura definida (Fig 3), o bico retornará à posição de origem e então se moverá para cima da plataforma de impressão e extrusará o filamento, use uma pinça para remover o filamento de saída (Fig 4).
- **Etapa 4.** Quando o bico for movido para a cama quente e começar a imprimir, clique duas vezes no botão para abrir o menu **Babystep Z** (Fig 5), gire o botão lentamente para ajustar a altura de impressão plataforma, observe a distância do bocal ao leito, até que a distância fique boa (Fig 6).
- **Etapa 5.** Aguarde o término da impressão (Fig 7), e espere o viveiro esfriar (Fig 8), e então remova o objeto impresso do viveiro (Fig 9).


#### Imprimir um arquivo de teste multicolorido
###### (https://www.youtube.com/watch?v=iddKadfrdjw)
As etapas para impressão multicolorida e impressão em cor única são basicamente as mesmas, mas antes de iniciar a impressão, extrude alguns filamentos de todas as extrusoras para confirmar se o hot end funciona normalmente.
- **Etapa 1.** Insira o cartão SD no soquete de cartão SD da impressora.
- **Etapa 2.** Aqueça o bico e faça a extrusão de alguns filamentos. **Preparar>>Filamento: *Bocal de pré-aquecimento: 200* -> *Extrusora: Todos* -> *Carregar lentamente***.
- **Etapa 3.** Clique no ÍCONE “Imprimir” no painel de controle e escolha ***M4_4CTest.gcode***, clique no botão para iniciar a impressão.
- **Etapa 4.** Ajuste a distância do bocal ao leito.
- **Etapa 5.** Aguarde o término da impressão.

-----
### :fireworks: Parabéns!
Após imprimir os primeiros trabalhos, você terá um entendimento básico de como funciona a impressora 3D. Em seguida, você pode imprimir outros arquivos de teste ou fatiar seu próprio modelo 3D e usar a máquina para imprimi-lo.
É recomendável que você baixe e instale o software de fatiamento e leia o guia do usuário do software de fatiamento para saber como usá-lo. Para obter detalhes, consulte o [:book: **Guia de fatiamento**](https://github.com/ZONESTAR3D/Z9/tree/main/Z9V5/Z9V5-MK6/4.Slicing).

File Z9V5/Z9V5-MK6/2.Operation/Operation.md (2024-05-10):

## <a id="choose-language">:globe_with_meridians: Choose language </a>










----
## Operation guide
Before start printing, you need to level the hot bed (fine tune the distance between the nozzle and the printing platform) and load the filaments into the extruders and hot end.
## Leveling the hot bed
#### :warning: For a FDM 3D printers, the distance between the nozzle and the hot bed is very important when printing the first layer. If the distance is too close, the filaments cannot flow out of the nozzle, and even damage the nozzle and the hot bed. If the distance is too far, the filaments cannot pasted on the hot bed, the next layers cannot be stacked correctly and cause printing fail.     
###### (https://www.youtube.com/watch?v=jNf98S0u2VQ)
- **Step 1.** Power on the 3d printer and then do ***Prepare>>Auto Home>>Home All*** on LCD MENU, wait the hotend go to the HOME position. 
- **Step 2.** Tighten the hand nuts under the bed to move down the bed to the lowest position (Fig 1).
- **Step 3.** Do ***Prepare>> Bed leveling>> Point 1*** on control panel(Fig 2), the nozzle will go to the corners of the bed, loosen the hand nuts under the hotbed (Fig 3) and let the nozzle almost touch the hotbed (Fig 4). Continue to do ***Point 2/3/4*** until all of the 4 corners has been leveled.
- **Step 4.** Repeat Step 3 and do 2 ~ 3 rounds, until all of the four corners at the same height.   


----
### Load filaments
###### (https://www.youtube.com/watch?v=1rr4dXRxKc4)   
This printer is equipped with four extruders and one 4-IN-1-OUT color mixing hot end. The extruders and the hot end are connected by a filament guide (PTFE tube). ***Before printing, you need to load all 4 filaments to the extruders and feed them into the bottom of the hot end.*** 
- **Step 1.** Do ***Prepare>>Auto Home>>Home All*** on control panel, and then do ***Prepare>>Temperature>> Preheat PLA***, waiting nozzle temperature reached to 190 ℃ (Fig 1).
- **Step 2.** Use a diagonal pliers to cut off the head of filament (Fig 2), and then press the handle of the extruder#1 and insert filament, push the filament until you can see the filament in the PTFE guide (Fig 3). Rotate the gear of extruder #1 (Fig 4), watch the filament until it entered bottom of the hot end. 
- **Step 3.** Using the same method as in step 2 to load the filaments to extruder#2 ~ extruder#4, watch the filaments until them entered the bottom of hot end.
- **Step 4.** Slowly rotate the gear of extruder#1 ~ extruder#4 one by one and watch the nozzle, until you can see the filament flowed out from the nozzle(Fig 5).


----
### Print your "Hellow World"" works
#### Print a single color test file
###### (https://www.youtube.com/watch?v=NbVy8NjKt_s)    
- **Step 1.** Insert the SD card to the SD card socket on the printer (Fig 1).
- **Step 2.** Click ***Print*** ICON on the control panel and choose ***xyz_cube.gcode*** (Fig 2), click the knob to start printing.
- **Step 3.** Wait until the hotend and hotbed is reached to the setting temperature (Fig 3), the nozzle will home to the origin position and then move to above of the printing platform and extrude the filament, use a tweezers to remove the outflow filament (Fig 4).
- **Step 4.** When the nozzle moved to the hot bed and start to print, double click the knob to open a **Babystep Z** menu (Fig 5), rotate knob slowly to fine tune the height of printing platform, watch the distance from nozzle to bed, until the distance goes well (Fig 6). 
- **Step 5.** Wait the printing finished (Fig 7), and wait the hotbed cool (Fig 8), and then remove the printed object from the hotbed (Fig 9).


#### Print a multi color test file
###### (https://www.youtube.com/watch?v=iddKadfrdjw)    
The steps for multi-color printing and single color printing are basically the same, but before starting printing, please extrude some filaments from all extruders to confirm that the hot end work normally.
- **Step 1.** Insert the SD card to the SD card socket on the printer.
- **Step 2.** Heat the nozzle and extrude some filamen. **Prepare>>Filament: *Preheat Nozzle: 200* -> *Extruder: All* -> *Load Slowly***.
- **Step 3.** Click “Print” ICON on the control panel and choose ***M4_4CTest.gcode***, click the knob to start printing.
- **Step 4.** Fine tune the distance from nozzle to bed.
- **Step 5.** Wait the printing finished.

----
### :fireworks: Congratulate! 
After printed the first works, you have a basic understanding of how the 3d printer works. Next, you can print other test files or slice your own 3D model and use the machine to print it out.    
It is recommended that you download and install the slicing software, and read the user guide of the slicing software to know how to use it,for details, please refer to the [:book: **Slicing Guide**](https://github.com/ZONESTAR3D/Z9/tree/main/Z9V5/Z9V5-MK6/4.Slicing).

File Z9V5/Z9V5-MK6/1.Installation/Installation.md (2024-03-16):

# Z9V5Pro-MK6 Installation guide

-----
## [:clapper: Installation video tutorial](https://youtu.be/TGHUVzV1Pg4)

-----
## :warning:ATTENTION:warning: 
### :beginner: Please strictly follow the standard operation when installation.
### :children_crossing: Please put the printer away from the reach of kids.
### :underage: Must be guided by adults when children are installed or used.
### :zap: Take care when installation, to avoid electrical shock hazards.
### :hotsprings: Hotend has high temperature even the printer stop working.
### :hotsprings: Hotbed has high temperature even the printer stop working.
### :smoking: Please keep well-ventilated condition! May produce toxic gases when printer working.

-----
## Parts list
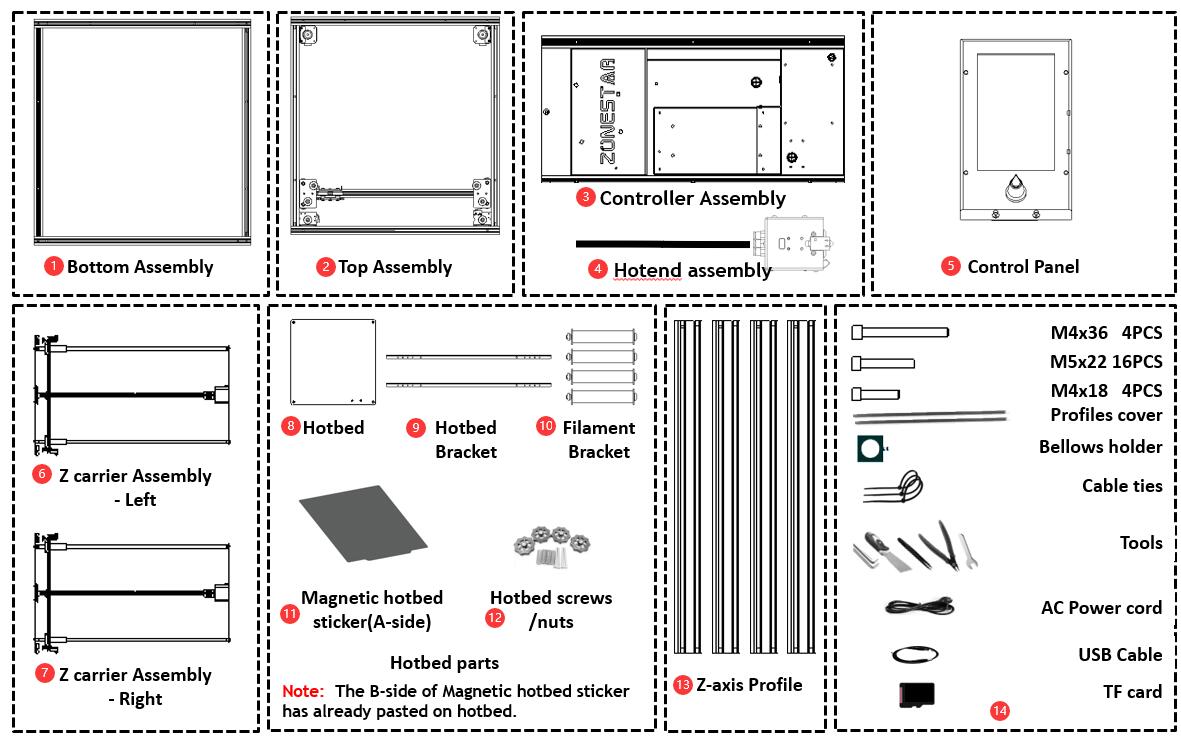
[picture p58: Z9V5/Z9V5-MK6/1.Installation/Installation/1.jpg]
    
>
     1. Bottom Assembly            2. Top Assembly               3. Controller Assembly          4. Hot end assembly          
     5. Control Panel              6. Left Z carrier Assembly    7. Right Z carrier Assembly     8. Hotbed                       
     9. Hot bed Bracket           10. Filament Bracket          11. Magnetic hotbed sticker     12. Hotbed screws /nuts       
    13. Z-axis Profile            14. Others (screws, tools, cable tie, SD card, Spare parts, etc.)

-----
## Before installation
### Machine View (after installed)
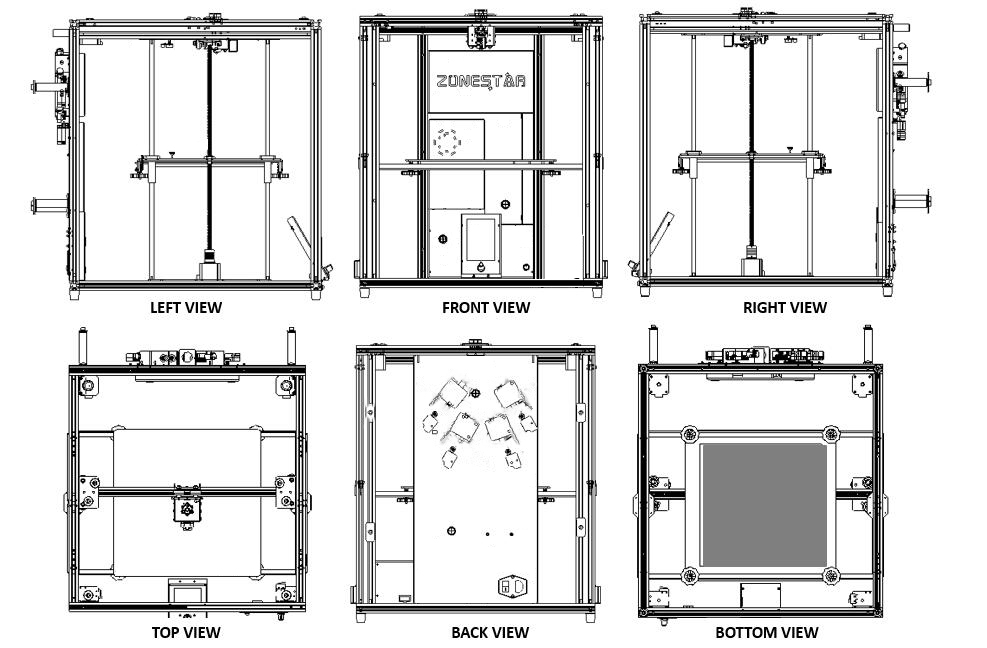
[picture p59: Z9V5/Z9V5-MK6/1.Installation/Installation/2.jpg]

### Installation direction
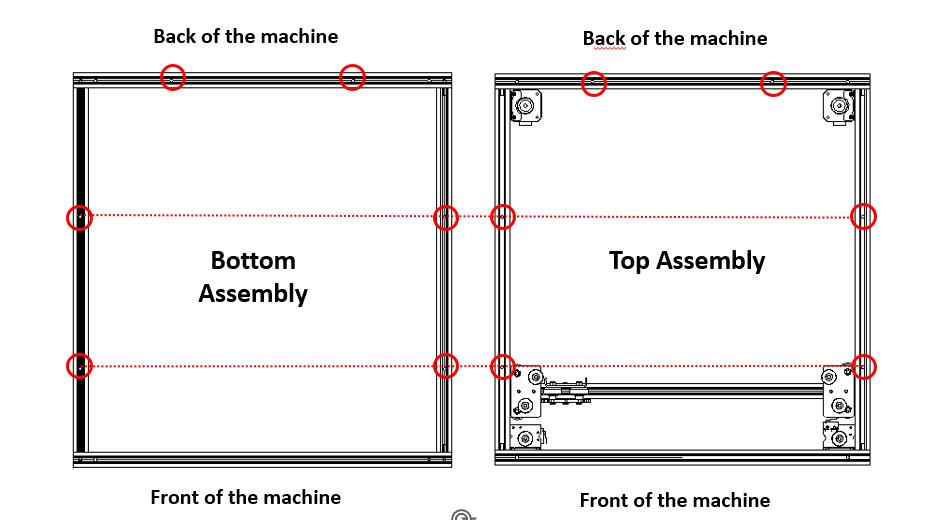
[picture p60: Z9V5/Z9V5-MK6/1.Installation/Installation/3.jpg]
     
### :warning: Pay attention to distinguish the front and back of the top and bottom assembly.     
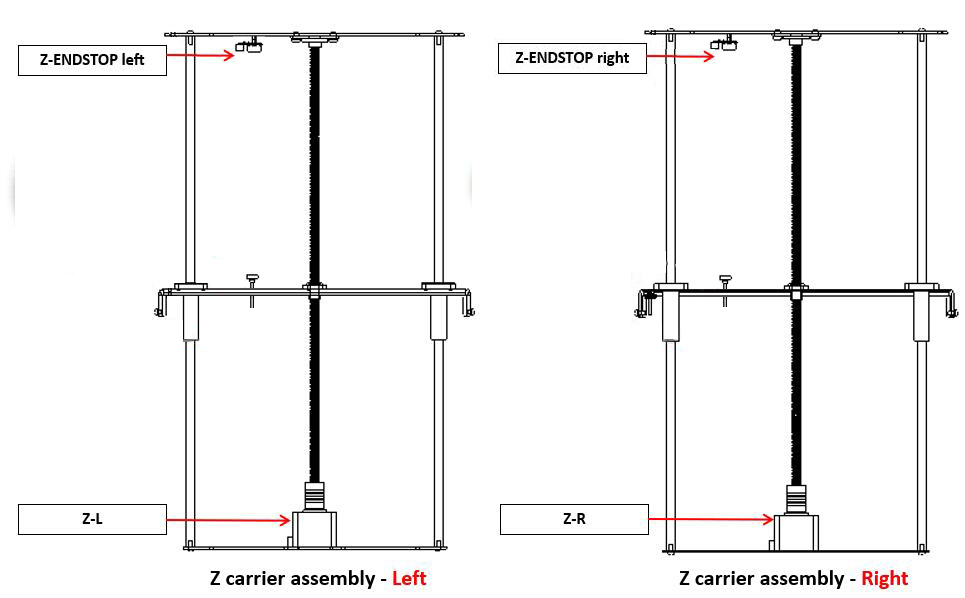
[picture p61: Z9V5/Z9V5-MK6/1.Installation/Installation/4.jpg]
    
### :warning: Pay attention to distinguish the left Z carrier assembly and the right Z carrier assembly.   

-----
## Assembly
### 1. Install Z profiles
#### Install 4 Z Profiles to the bottom assembly. Note that there is a hole on one of side of Z profile, this side should be toward to the upper. There is a hole next to the rubber foot pad of the bottom assembly, which is used to fix the Z-axis profile. Mount M5x22 screws from the bottom profiles upwards and secure to Z profile.
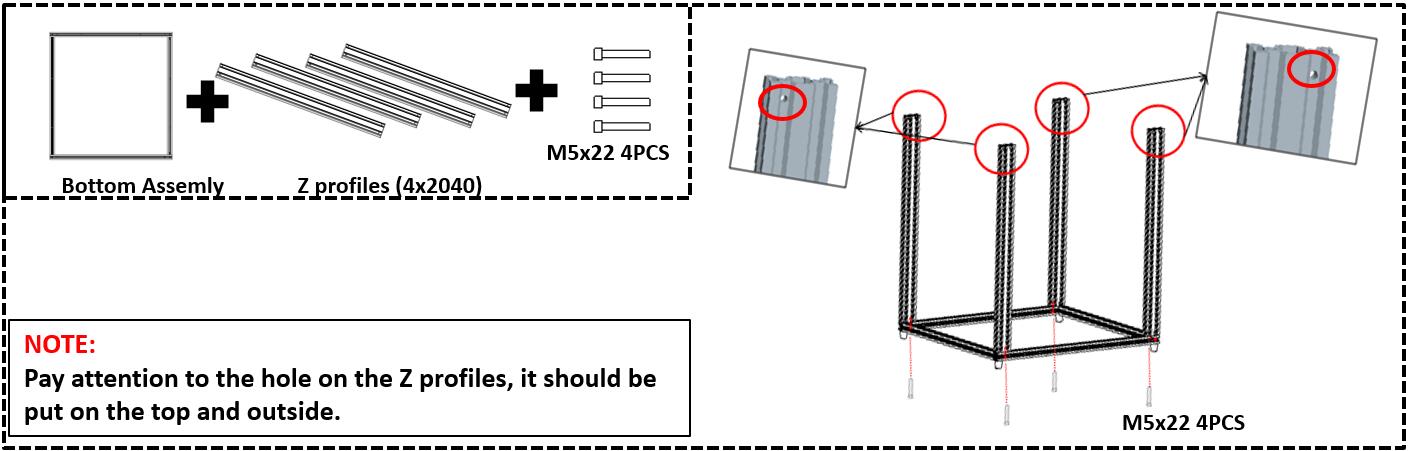
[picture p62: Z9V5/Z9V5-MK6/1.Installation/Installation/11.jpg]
          
### :warning: Pay attention to the hole on the Z profiles, it should be put on the top and outside.     
### 2. Install Left & Right Z carriers 
#### Install Left & Right Z carriers to the bottom assembly. Note that the side with a Z limit switch of the Z carrier should towards the back of the machine. Mount M4x18 screws from the bottom profile upwards and secure to the sheet metal of the Z carrier.
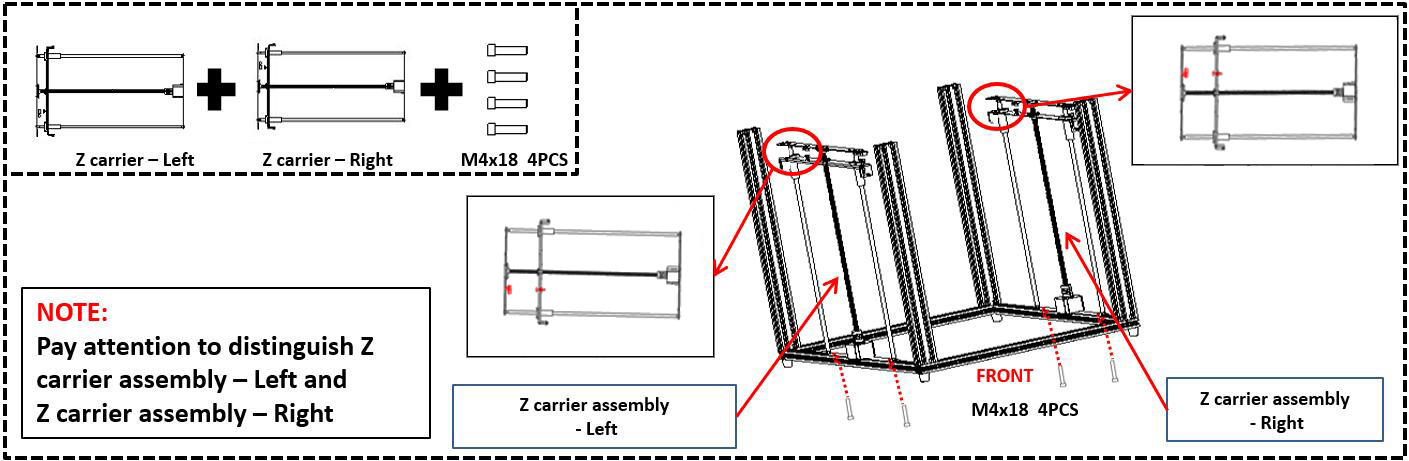
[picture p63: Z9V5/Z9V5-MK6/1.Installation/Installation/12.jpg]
       
### :warning: Pay attention to distinguish Left Z carrier assembly and Right Z carrier assembly.
### 3. Install top assembly
#### Place the top assembly (the side with motors on the back) on the Z-axis profiles, note that the screw cap of the Z carriers should be placed in the groove of the profile of top assembly. Two sides are fixed to the sheet metal of the Z carriers by using M4x36 long screws, use 4 PCS M5x22 screw to fix the top assembly and the Z-axis profiles, and use other 4 PCS M5x22 screws to fix the side of the Z profiles and the Y-axis profiles.
### :warning: Don't tighten these screws in this step.    
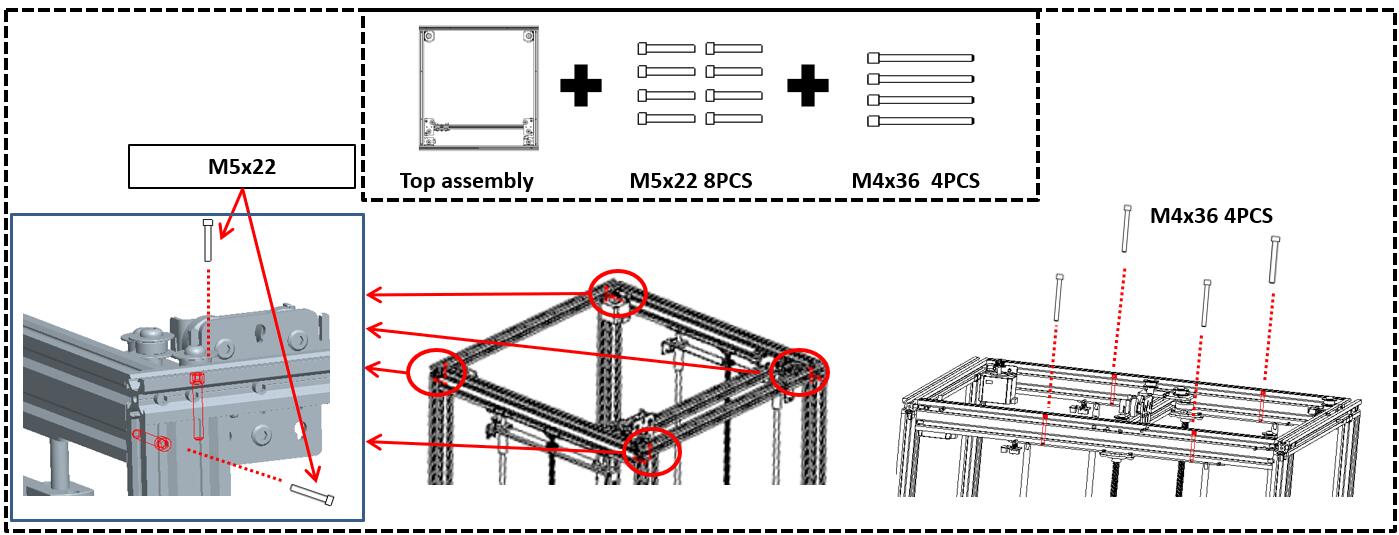
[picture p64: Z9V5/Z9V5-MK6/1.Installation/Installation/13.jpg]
       
### 4. Install controller assembly
#### 4.1 Put the control box assembly between the top assembly and the top assembly of the back of the machine, use 4 PCS M5x22 screws to fix it on the profiles.
#### 4.2 Tighten all those screws installed on step 3.  
#### 4.3 Install the bellows holder to the center of top-back profile.     
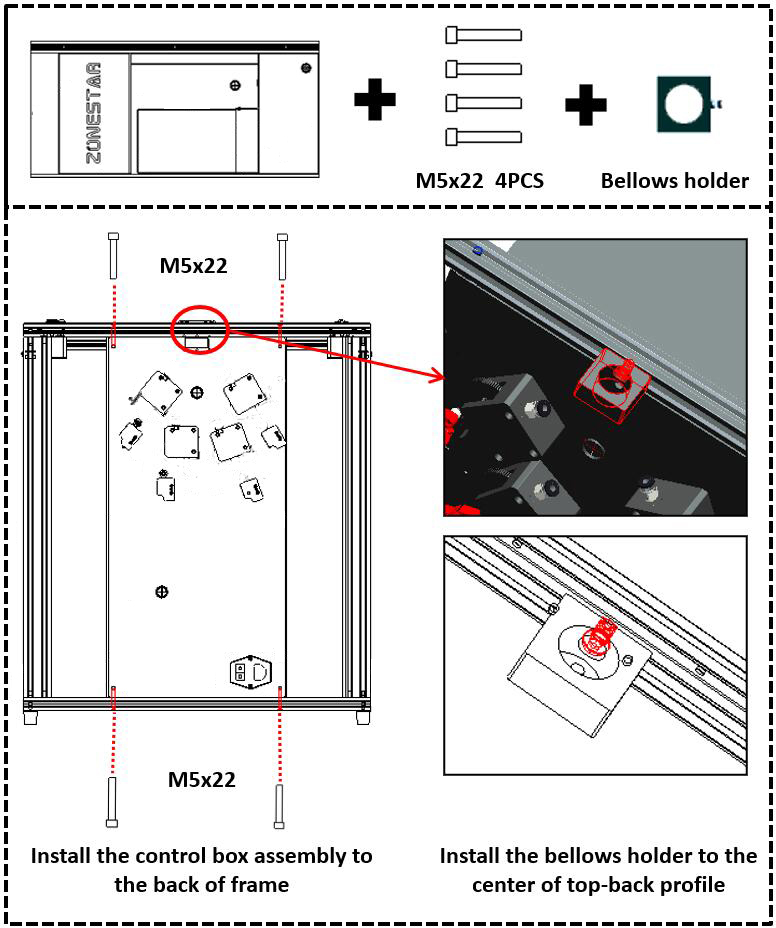
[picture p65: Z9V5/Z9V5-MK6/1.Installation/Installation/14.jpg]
   
### 5. Adjust the eccentric columns
#### 5.1 Adjust the eccentric columns (2 PCS on the left and 2 PCS on the right) under the Y carrier, and move the Y profile from front and back, ensure it can move smoothly and doesn’t shake.    
#### 5.2 Adjust the eccentric column under the X carriers, and move the X carriers from left and right, ensure it can move smoothly and doesn’t shake.    
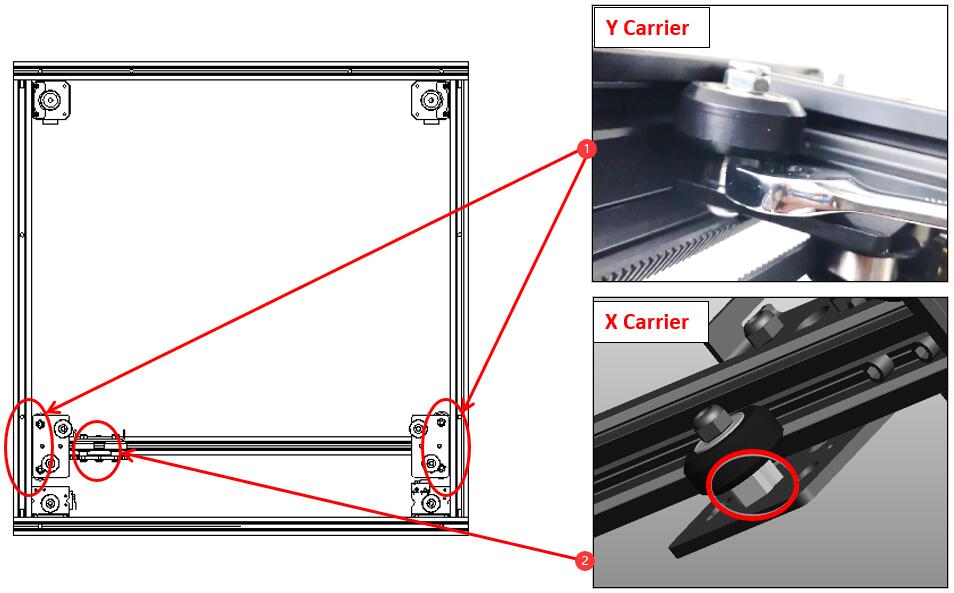
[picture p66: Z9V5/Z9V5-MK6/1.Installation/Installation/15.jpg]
   
### 6. Install hot bed parts
#### 6.1 Take down these M4 screws first on Z carriers metal pieces and then use these M4 screws to mount hot bed brackets on the Z carriers, 
#### 6.2 Install aluminum heat bed to the hot bed brackets, the springs should be placed between the heat bed and the bracket, install the hand nuts under the brackets.
### :warning: Note the the hotbed cable should be place to the right-back corner of the machine.  
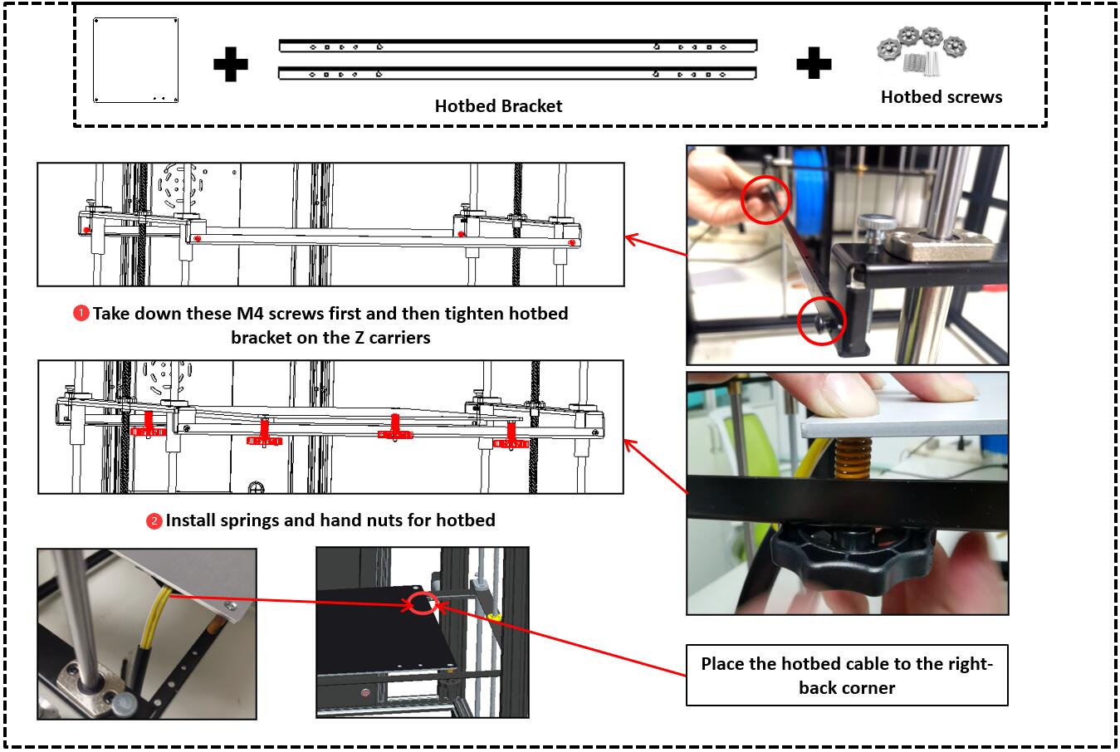
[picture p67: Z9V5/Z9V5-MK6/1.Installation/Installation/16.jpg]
  
### 7. Install control panel
#### Install control panel to the center of bottom-front profile.
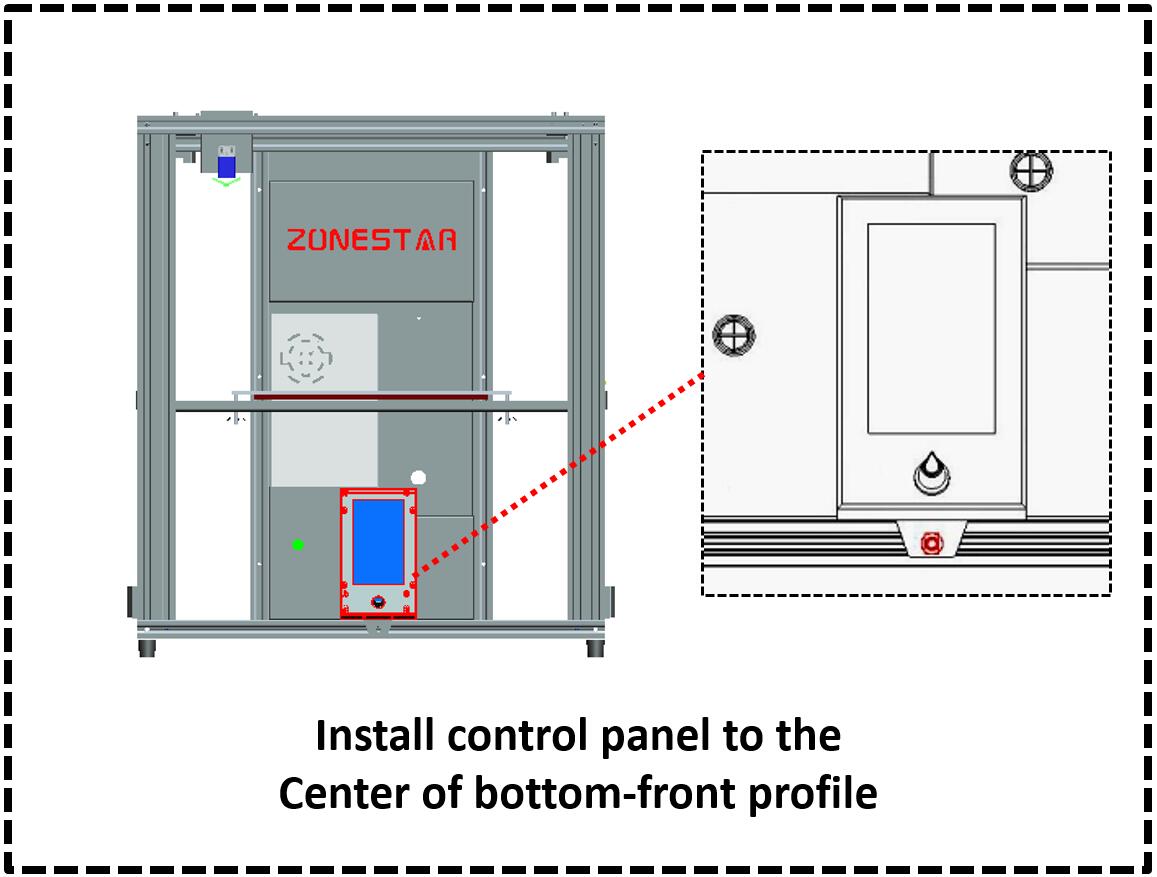
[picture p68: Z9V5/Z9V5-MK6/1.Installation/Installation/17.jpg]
  
### 8. Install filament holders
#### Install 4 sets of filament brackets to the back Z profiles.
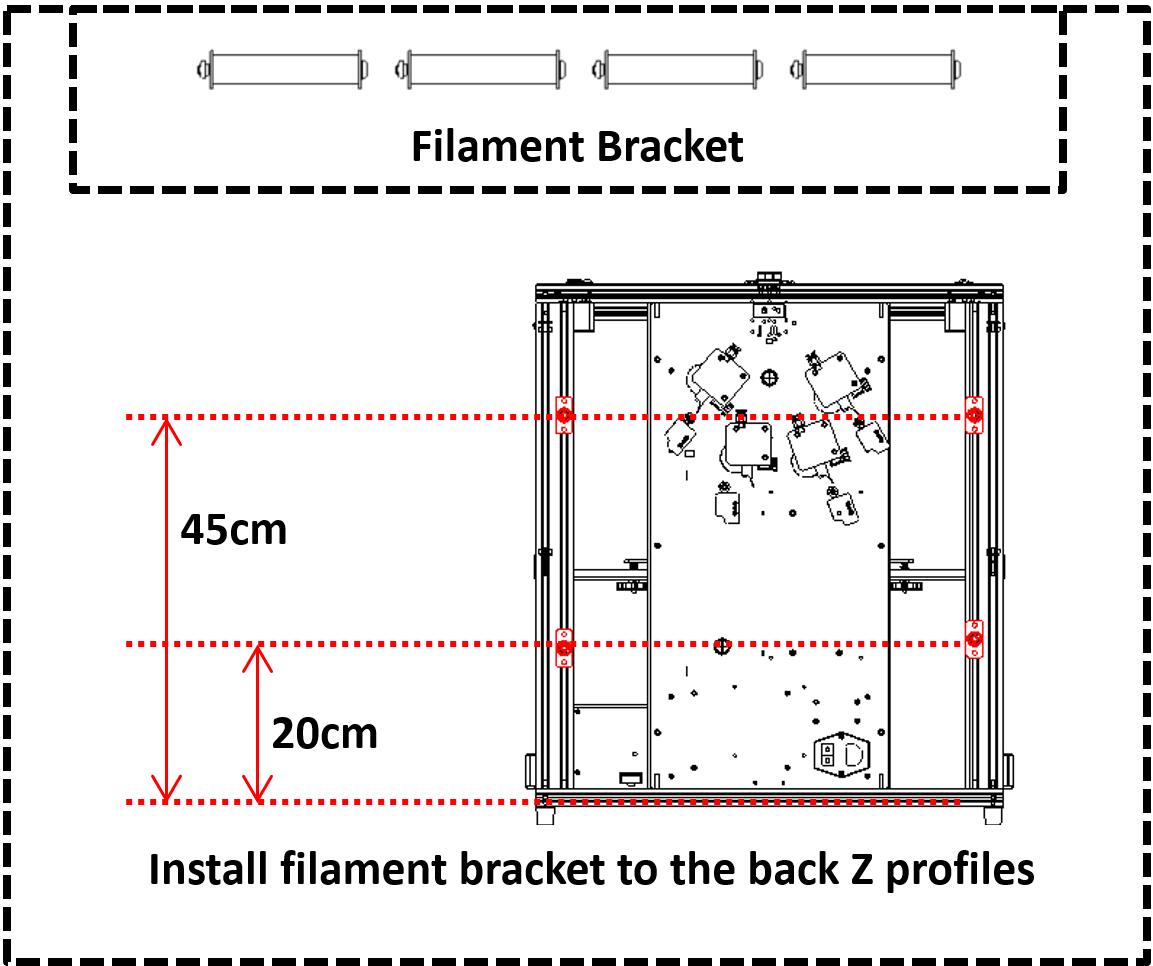
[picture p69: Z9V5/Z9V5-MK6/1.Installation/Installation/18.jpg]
  
### 9. Install hotend assembly
#### Loosen the 3 pcs of screws on the hot end assembly and then mount the hot end assembly to the X carrier.
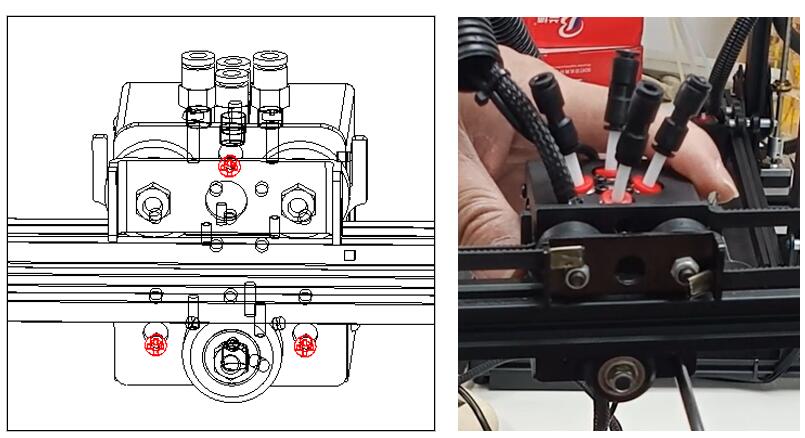
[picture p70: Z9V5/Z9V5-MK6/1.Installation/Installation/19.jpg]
  
### 10. Past the heat bed sticker
#### Place the "A side" of the magnetic hot bed sticker (that with PC film) on the hot bed (B side has already pasted on the heat bed).
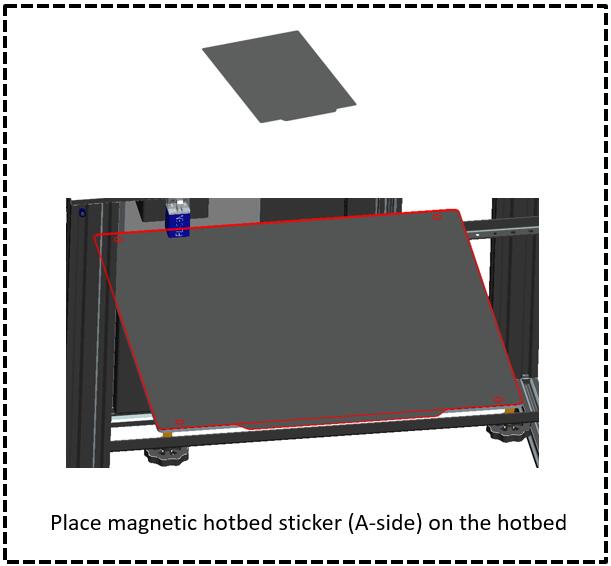
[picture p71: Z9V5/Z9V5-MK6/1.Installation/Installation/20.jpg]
  

-----
## :fireworks: Congratulate! 
Now the machine installation is announced to be completed, next you can arrange to wiring.      
- [**:book: Wiring Guide Online Document**](./Wiring.md).
- [**:blue_book: Wiring Guide pdf file**](./Wiring.pdf).

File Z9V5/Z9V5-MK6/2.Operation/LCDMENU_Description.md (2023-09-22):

# LCD Menu Description

-----
## Brief of the Control Panel 

### Intruduction of menu
  >
    1. Title bar          2. Menu bar       3. Status bar         4. Control knob
    5. Printing Menu      6. Prepare Menu   7. Setup Menu         6. Information Menu
### Operation of the knob
- **Press:**                  Execute command / Enter menu.
- **Rotate clockwise:**       Increase the value / Move to the next menu item.
- **Rotate anti-clockwise:**  Decrease the value / Move to the pervious menu item.

-----
## LCD Menu  

### Main Menu

  >
    1. LOGO                   2. Print from SD card            3. Prepare to print
    4. Machine Settings       5. Machine Information           6. Nozzle Temperature
    7. Hotbed Temperature     8. Printing Speed                9. Current Z position

### Printing status Menu (Hotend Type is “Non-mixing")

  >
    1. Titel                              2. Printing file name and Progress bar      3. Extruder Status and FAN Speed
    4. Printed time and Remain time       5. Set printing parameters                  6. Pasue&Resume Printing
    6. Stop Printing                      7. Nozzle Temperature                       8. Hotbed Temperature     
    9. Printing Speed                     10. Current Z position                      12.Status Message Bar

### Printing status Menu (Hotend Type is “Mixing")

  >
    1. Titel                              2. Printing file name and Progress bar      3. Extruder Mix Rate and Auto Mixing mode
    4. Printed time and Remain time       5. Set printing parameters                  6. Pasue&Resume Printing
    6. Stop Printing                      7. Nozzle Temperature                       8. Hotbed Temperature     
    9. Printing Speed                     10. Current Z position                      12.Status Message Bar

### Prepare Menu


| Level 1 | Level 2 | Description |
|:---:|:---:|:---|
| Auto Home |  HOME ALL |  HOME all axis at once |
| Auto Home |  HOME X |  HOME X axis |
| Auto Home |  HOME Y |  HOME Y axis |
| Auto Home |  HOME Z |  HOME Z axis |
| | | |
| Temperature |  Nozzle Temp |  Set Nozzle(hotend) Temperature |
| Temperature | Bed Temp |  Set Hotbed Temperature |
| Temperature | Fan Speed |  Set Extuder Cooler FAN speed |
| Temperature |  PreHeat PLA |  Set Nozzle/Hotbed at once (lower temperature for PLA filament)|
| Temperature |  PreHeat ABS |  Set Nozzle/Hotbed at once (lower temperature for ABS filament)|
| Temperature | Cooldown |  Stop heating Hotend and Hotbed at once |
| | | |
| Move | X |  Move X axis |
| Move | Y |  Move X axis |
| Move | Z |  Move X axis |
| Move | Extruder(n) |  Move Extruders (to feed/unload filament) |
| Move | Extruder All|  Move All Extruders (to feed/unload filament) |
| | | |
| Filament |Preheat nozzle  |  Preheat the nozzle to the setting temperature |
| Filament |Extruder |  Choose which extruder to operate |
| Filament |Slowly length |How long filament be load/unload while did “Slowly Load" & “lowly Unload”|
| Filament |Quickly length  |How long filament be load/unload while did “Quickly Load" & "Quickly Unload“|
| Filament |Slowly Load |Load filament slowly |
| Filament |Slowly UnLoad |Unload filament slowly |
| Filament |Quickly Load |Load filament quickly |
| Filament |Quickly UnLoad  |Unload filament quickly |
| | | |
| Bed Leveling |Point 1 |Do leveling at the bed corner 1 |
| Bed Leveling |Point 2 |Do leveling at the bed corner 2 |
| Bed Leveling |Point 3 |Do leveling at the bed corner 3 |
| Bed Leveling |Point 4 |Do leveling at the bed corner 4 |
| Bed Leveling |Catch Probe Z-offset|Auto Catch the probe Z offset (Display only “Auto levleing" is ON)|
| Bed Leveling |Adjust the probe Z offset|Auto Catch the probe Z offset (Display only “Auto levleing" is ON)|
| Bed Leveling |Auto leveling|Do auto leveling measure (Display only “Auto levleing" is ON) |
| | | |
| Language | EN/ES/RU/FR/PT | Set menu language |
| Disable Steppers | | Turn off the power supply to motors |
| Power off | | Power off the printer |

### Control Menu



#### Control Menu Description
| Menu 2 | Menu 3 | Description |  
|---|---|---|
| Mixer* |Mix |Set mix rates of each extruder and commit to V-TOOL |  
| |Gradient(ON/OFF) |Start a Gradient mix printing and set paremeters |  
| |Random (ON/OFF) |Start a Random mix printing and set paremeters |  
| |Current V-TOOL |Set current(working) V-TOOL |  
| Configre |Auto Retract |Set Auto Retraction parameters |  
| |Runout Sensor |Turn ON/OFF filament run out detection feature |  
| |Auto Unload |Auto unload filament when printing is abort (only works on Non-mix color hot end)  |  
| |PowerLoss Recovery |Turn ON/OFF Power lost Recovery feature |  
| |Auto Shutdown |Turn ON/OFF idel auto shut down feature |  
| |WiFi |Turn ON/OFF WiFi feature |  
| |WiFi BaudRate |Set WiFi BaudRate (Need restart printer and change the WiFi module BaudRate) |  
| |Hotend Type |Set Hot end types (according to your hot end type) |  
| |Extr. Sequence |Change Extruder Sequence (only work on Non-Mixing Color hotend) |  
| |Home Z offset |Set the Z HOME offset |  
| |Auto Leveling |Turn ON/OFF bed auto leveling feature |  
| |Active Auto Level  |Active bed auto leveling correct when printing |  
| |Hotend PID |Set the hotend PID parameters |  
| Motion |Feedrate |Set printing speed limiting parameters |  
| |Acceleration |Set acceleration limiting parameters |  
| |Jerk |Set Jerk parameters |  
| |Step/mm |Set Steps/mm parameters of stepping motors |  
| Preheat PLA |Nozzle Temp |Set nozzle temperaturewhen do “Preheat PLA" on Prepare menu |
| |Bed Temp |Set Bed temperature when do “Preheat PLA" on Prepare menu |
| |Fan Speed |Set FAN speed when do “Preheat PLA"o n Prepare menu |
| |Store Settings |Store above settings |  
| Preheat ABS |Nozzle Temp |Set nozzle temperaturewhen do “Preheat ABS" on Prepare menu |
| |Bed Temp |Set Bed temperature when do “Preheat ABS" on Prepare menu |
| |Fan Speed |Set FAN speed when do “Preheat ABS" on Prepare menu |
| |Store Settings |Store above settings |  
| Store Settings | |Save the settings |  
| Load Settings | |Load the settings from NVRAM (maybe it has been changed by Gcode command) |  
| Restore Default  | |Reset NVRAM settings to the factory status |  

*Display only when “Control>> Configure >>Hotend type: mixing" see “Control>>Configure"

### Tune Menu
:warning: Tune menu only display when printing from SD card.

##### Tune Menu Description

| Menu item | Description |  
|---|---|
| Speed |Set the ratio of printing speed |
| Flow Rate |Set the flow rate of extruder |
| Nozzle Temp |Set Nozzle temperature |
| Bed Temp |Set Bed temperature |
| Fan Speed |Set Extruder FAN Speed |
| Z Offset |Tune Z offset |
| Mixer |Set mixer,refer to “Control>> Mixer" Menu (only display while “Hotend type is Mixing")  |
| Configure |Tune ON/OFF parts of configurations features, refer to “Control>> Configure" Menu |

---
#### :link: [How to upgrade firmware of DWIN LCD Screen](https://github.com/ZONESTAR3D/Upgrade-kit-guide/tree/main/TFT-LCD/LCD-DWIN#update-image-data-of-dwin-lcd)

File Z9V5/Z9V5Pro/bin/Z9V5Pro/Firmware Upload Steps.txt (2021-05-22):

Firmware Upload Steps:
1. Download the zip file and unzip it
2. Copy firmware.bin to the root directory of Micro-SD card
3. Power off the printer and plug the Micro-SD card into socket on control board
4. Power on the printer, push the power button and wait about 30 seconds
5. Do the below step on LCD screen to initialize EEPROM after upload firmware:
MENU>>config>>Restore Defaults

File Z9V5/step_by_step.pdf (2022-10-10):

step_by_step.md | 10/10/2022

1 / 2

## Step by Step Guide

If you're a beginner with 3D printers, with so much documentation to read, you might not know where to start. Don't worry, we'll go into the details of these documents next step by step. In a word, you need to do 4 steps Install the machine - Printing test file - Slicing your own 3d file - Printing your 3d file.
First at all, please download the documents and save to your PC from this link. (https://github.com/ZONESTAR3D/Z9/tree/main/Z9V5/Z9V5-MK4#download-z9v5-mk4-files)
Step 1. Install the machine
1.1 Installation. Refer to the | installation guide and | installation video tutorial (https://youtu.be/Xa3Q1m6HbDI) to complete
the installation of the machine. The Z9V5 has a high pre-assembled ratio, so installation is very simple. 1.2 Wiring. the process of wiring is basically to insert the plug into the corresponding socket. What you need to pay attention is to make sure the plug is fully inserted into the socket. Especially for those 2PIN docking sockets that sometimes make poor contact. In addition, for the wiring of the print head (hot end), please note that there are several sockets of the same type but different colors, please pay attention to plug them according to the color of the socket.
1.3 Power ON. When wiring is complete, you can turn on Z9V5. (https://youtu.be/xTlMHtxkGoY) Please note in particular that the Z9V5 has 2 power switches. the one is AC switch(the red switch on the back of the machine) and another is DC switch(a round metal push button switch on the front of the machine control box), you need to turn on the AC switch first and then press and hold the DC switch for a few seconds to turn on Z9V5.
1.4 Simply Test. After power on, you can operate the menu on the LCD screen (LCD Menu description) to verify whether the machine can work normally. Usually this involves several steps:
1.4.1 Prepare>>Auto Home>>Home All. This step is to make the print head of the machine return to the origin.
1.4.2 Prepare>>Temperature>>Preheat PLA. This step is to check the hot end and the hot bed can be heated normally.In this step, when the temperature of the nozzle exceeds 60 degrees, you should see a fan on the right side of the print head (hot end) spin up, this is the hot end cooling fan.
1.4.3 Prepare>>Temperature>>FAN. After pressing the knob and setting the fan speed (set to 255), you should now be able to turn the fan on the left side up as well.
After these 3 steps, it is basically determined that the machine are working normally, you can proceed to the following steps. If you find that any part is not working properly, please double check the wiring, or to do a auto testing (Refer to machine auto testing video turorial). (https://youtu.be/Mf92BlmKA0A) 1.5 Bed Level - leveling 4 corners of the bed. Before printing the test file, you need to do a simple bed leveling to set the height between the nozzle and the bed (printing platform), so that the filament can be sticked on the bed well. Please refer to Bed leveling video tutorial (https://youtu.be/nxzB7ho1kNo) to do it.
Step 2. Print test 3d model

FDM 3D printers can only recognize gcode files, we need to copy the gcode files to the SD card, insert the SD card into the SD card slot of the 3D printer, and then start to print.

2.1 Prepare gcode file - one color. Locate the xyz_cube.gcode file from your downloaded files or download it directly and unzip it on PC, and then copy the xyz_cube.gcode to SD card. Plug the SD card to the SD socket of machine.

step_by_step.md | 10/10/2022

2 / 2

2.2 Load filament - one color. Refer to this video tutorial (https://youtu.be/6aTF5QnFhi4) to load filament to the extruder and hotend.
2.3 Print from SD card - one color. Move item to Print item on LCD screen and click the knob and choose xyz_cube.gcode file, click knob to start print.
2.4 Fine tune nozzle height. Wait the nozzle and hotbed heating, and when starting to print the first layer, double to click the knob of LCD screen to fine turn the distance from the nozzle to the bed, and then wait it to finish.
2.5 Prepare gcode file. Locate the Z9E4_4CTest.gcode file from your downloaded files or
download it directly and unzip it on PC, and then copy the Z9E4_4CTest.gcode to SD card. Plug the SD card to the SD socket of machine.
2.6 Load filaments - 4 colors. Refer to this video tutorial (https://youtu.be/FyHrAMytlT8) to load 4 color filaments to the extruders and hotend.
2.7 Print from SD card - 4 colors. Move item to Print item on LCD screen and click the knob and choose Z9E4_4CTest.gcode file, click knob to start print.
2.8 Check Preload. Wait the nozzle and hotbed heating, and check if the printer can print out 4 colors lines on the side of the hotbed.
2.9 Fine tune nozzle height. When the hotend moved to the center of the hotbed, double to click the knob of LCD screen to fine turn the distance from the nozzle to the bed. Wait until the printing is finished.
Step 3. Slicing your own 3d model

Obviously you will have the need to print your own 3D models. The process of converting a 3D model into a gcode file that can be printed on a machine is called slicing. You need to download and install the slicing software, then import the 3D model file (stl, obj, AMF, etc.) and complete the slicing, and finally copy the generated gcode file to the SD card and print it on the machine. Our recommended slicing software is PrusaSlicer. For detailed instructions, please refer to 4. Slicing. (https://github.com/ZONESTAR3D/Z9/tree/main/Z9V5/Z9V5-MK4#download-z9v5-mk4-files)
Several of the most famous free 3D model download websites:

thingiverse (https://www.thingiverse.com/)
printables (https://www.printables.com/)
youmagine (https://www.youmagine.com/)
Step 4. Printing your own 3d model

Once you are done slicing, copy the obtained gcode files to your SD card, then you can print them out like in the step 2. (https://github.com/ZONESTAR3D/Z9/tree/main/Z9V5/Z9V5-MK4#2-test-gcode)
Step 5. To use advanced features

After you fully understand all the basic use of the machine, you can try some advanced functions of the machine. For details, please refer to Advance features. (https://github.com/ZONESTAR3D/Z9/tree/main/Z9V5/Z9V5-MK4#2-test-gcode)

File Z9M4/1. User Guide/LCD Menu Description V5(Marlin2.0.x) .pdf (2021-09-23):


# Brief of LCD Menu ZONESTAR 3D Printer DIY Kit

# (Base on Marlin 2.0.x)

# Ver: 5


# LCD screen and Keypad

LCD12864 with knob

## Operation and Function

Operation | Function
Clockwise rotation | Menu item+ / Value +
Counterclockwise rotation | Menu item+ / Value -
Push | Open Menu /Enter


fig | Description
1 | Current hotend temperature
2 | Setting hotend temperature
3 | Current hotbed temperature
4 | Setting hotbed temperature
5 | Current X Y Z position
6 | Extrude fan speed
7 | Multiple of print speed
8 | SD card print progress
9 | Status message
10 | mix rate of extruders
11 | Current Virual Tool Number or Auto Mix Mode

State menu description

# Menu description

Menu | Sub-Menu | Description | Remark
| Info Screen | Return to info menu
| Motion | Prepare Menu | Only shows on ideal status
| Pause Print | Pause Printing | Only shows on printing
| Stop Print | Stop Printing | Only shows on printing
| Tune | Tune parameter when printing | Only shows on printing/Motion
| Temperature | Control Menu
| Mixer* | Mixing Settings | Only available in mixing printer.
| Configuration | Set the printer parameter
| Change Filament | A wizard to help change filament
| About printer | Printer infomations
| Change Media | Press it before remove the SD card from control board | Only shows on ideal status
| Switch Power off | Power off the printer (only control board) | Only available has power button
| Print From Media | Press it to start to print from SD card. | Only shows on ideal status
Pop Menu | Babystep Z | double click the knob to open when printing | Only available when printing

Main Menu

*:

# Menu description

Motion

| Move Axis | Move X/Y/Z/Extruder motor | Need to heat nozzle before moving extruder
| Auto HOME | Do homing for all X/Y/Z
| HOME X/Y/Z | Homing X/Y/Z separately
| Level Corners | Move the nozzle to near the corners of hotbed | Adjust the screws under the bed to level it
| Catch Z probe offset | Catch the probe Z offset
| Level bed | Do a bed auto levling processing | Only for bed leveling sensor installed
| Probe Z offset | Adjust probe Z offset
| Bed leveling: Off(ON) | If a Bed leveling has done | Apply the Z axis error when show “ON”
| Disable Motor | Turn off the power of stepper motors
Temperature | Nozzle | Set nozzle temperature
| Bed | Set bed temperature
| Fan Speed | Set extruder FAN speed | Cooling fan is control automatically
| Preheat PLA/ABS | Preheat the hotbed and/or hotbed
Mixer | Active V tool | Set the current work V Tool | These menu only showed when the printer has mixing feature, about the detail, please refer to
| | Set Mixing parameter setting | the mixing feaure user guide. Mix
| Gradient: disable | Set Gradient mixing parameters
| Random Mix: disable | Set Random mixing parameters

# Menu description

Configuration

| Advanced Settings
| Run out sensor: On/Off | Turn on/off the filament run out detection feature | * Refer to “Filament Run out feature”
| Outage Recovery: On/Off | Turn on/off power loss recover feature | * Refer to “Power loss Resume feature”
| Preheat PLA/ABS Conf | Set preheat parameters
| Store Settings | Store the configuration to NVRAM of control board | Do it after you modified parameter!
| Load Settings | Load the NVRAM setting to the printer
| Restore Default | Reset the setting to the default
Tune | Speed | Adjust the print speed | Percentage of speed based on gcode
| Nozzle | Nozzle temperature
| Bed | Hotbed temperature
| Fan Speed | Extruder fan speed
| Flow | Extruder flow rate | Percentage of flow value based on gcode
| Babystep Z | Fine tune the Z height

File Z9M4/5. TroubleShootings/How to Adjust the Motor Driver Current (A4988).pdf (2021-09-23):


56

WARNING!! Please pay attention to the direction of the motor driver module, incorrect direction will damage the control board!!!!

You may need to adjust the drive current because a couple of reasons, for example, difference of the stepper motors, the hot bed weight, etc., you can rotate the potentiometer on the driver module to adjust the current.
NOTE: Too small drive current may cause lost step or abnormal noise. Too big current may damage the driver module because it is over heat!
Recommended current of stepper motors:
X Y& Z motor: 0.8A
Extruder motor: 0.6A (for Titan extruders)
If you want to adjust the current of the motor driver module, please measure the voltage (Vref) on the potentiometer with a multimeter (as below picture), DC Voltage Gears.
For 4988 driver module:
I motor = Vref * 1 . 25

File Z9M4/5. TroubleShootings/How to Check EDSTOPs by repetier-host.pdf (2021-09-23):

## Check ENDSTOPs by Repetier-Host

Prepare:
Step 1: Install Repetier-host to your PC (NOTE: DONOT USE Repetier-Severice)
Step 2: Connect the printer to PC by USB cable.
Step 3: Set the communication setting, then click connect button on Repetier-host.

About these steps, please refer to the Repetier-host user guide in the SD card. Download link: https://www.jianguoyun.com/p/DdgqMLMQyoP1BxjC56cD

Click Log to open the log window; Choose Manual Control , input M119 and then click send

## Check ENDSTOPs by Repetier-Host


Then you can see the ENDSTOP status in the LOG window

Press the ENDSTOP by hand and check if it can work well

Doesn’t click | Clicked

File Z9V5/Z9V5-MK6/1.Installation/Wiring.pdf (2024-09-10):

Wiring.md | 2024-09-10

# Z9V5-MK6 wiring guide

## Wiring video tutorial (https://youtu.be/tQQNLDOpdQU)

## Electronics parts

Please refer to the following figure to understand the location and name of the electronic components of the machine.


1. X motor (on the left/back) 2. X ENDSTOP (on the left/front) 3. Y ENDSTOP (on the right/front) 4. Y motor (on the right/back)
5. Left Z ENDSTOP | 6. Right Z ENDSTOP | 7. Cable for Heat
bed | 8. Left Z motor
9. Right Z motor | 10. LCD Screen (Control Panel) | 11. Micro-SD card
socket | 12. 110V/220V power select switch
13. Hole for USB cable | 14. USB connector | 15. DC Power Button
16. AC power socket and switch

## Wiring Diagram

Plug the wiring connector to the connectors of the electronic component as shown in the following figure, incude:

X motor wire and X ENDSTOP
Y motor wire and Y ENDSTOP
Left and right Z motor wire and Z ENDSTOP
Hot bed cable (power and temperature sensor)
LCD screen
Hot end assembly (Note: Hot end wires has already connected before the kit leaving factory.)


## Layout the wires

Put the wires to the profile grooves, cover with profile plastics strips. Tie the wires to the profiles after connected.

Be careful not to damage the insulation of wires when puting the motor cables to the profile grooves.


## Confirm the wiring

Confirm all wires are properly connected to the connectors.

Confirm the X/Y axis move smoothly by moving the "print head" manually.

Confirm the motor shaft has fixed with the lead screws properly by rotating both of the Z couplings manually.

Confirm the Z-axis limit switch adjustment knob and the hot bed screw have been adjusted to the specified position.


Confirm the AC voltage select switch of the power supply has been set to the correct position.

## Power on the machine

1. Connect one end of the power cord (female base) to the printer, and then connect the other end of the power cord to your power outlet. Turn on the AC power switch of the 3d printer.
2. Push and hold the DC power button, until you can see the LCD shows "logo screen", release the DC power button.

Tips: If you need to power off the printer, please turn off the printer on LCD screen first and then turn off the AC power switch.

## Final inspection

Now you have completed the wiring, but please follow the steps below to perform a simple inspection before using the machine.

1. Power on the printer.
2. Rotate and press the knob on the control panel (LCD screen) to check if the control panel is working properly.
3. Use the knob to move the menu "Prepare>>Auto Home>>Home All", and press the knob to do. The machine will follow these steps to operate:
The printing platform move down a few millimeters.
The Y-axis move forward until it reaches the Y ENDSTOP (a limit switch on the top-right of the machine).
The print head move to the left until the housing of the print head touches the X ENDSTOP (a limit switch on the top-left of the machine).
The printing platform move upwards until the Z-axis height adjustment screws touches the Z ENDSTOP (limit switch on the top of Z carrier).
If the machine doesn't work properly, please refer to the Troubleshooting Online Document to check it first. (https://github.com/ZONESTAR3D/Z9/tree/main/Z9V5/Z9V5_FAQ#faq-for-z9v5)
4. Use the knob to move the menu "Prepare>>Temperature>>Preheat PLA", and press the knob to do. And then watch the hot bed and hot end temperature shows on LCD screen, they will rise up to the setting temperature.
5. Power off the printer after finish the above steps.

LCD Menu description Online Document. (https://github.com/ZONESTAR3D/Z9/tree/main/Z9V5/Z9V5-MK6/2.Operation/LCDMENU_Description.md)
LCD Menu description pdf file.

## Congratulate!

Now, you have completed the wiring. Next, please refer to the Operation manual to make necessary adjustments to the machine and complete several printing tests to familiarize yourself with the operation of the machine.

Operation Manual Online Document. (https://github.com/ZONESTAR3D/Z9/tree/main/Z9V5/Z9V5-MK6/2.Operation/Operation.md) Operation Manual pdf file.

Appendix: Hotend cable


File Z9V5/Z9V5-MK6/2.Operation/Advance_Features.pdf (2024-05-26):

Advance_Features.md | 2024-05-26

## Advance features

Contents

Bed auto leveling Feature
Power Auto Shutdown Feature Auto Mixing Feature
Filament Run Out Detect Feature Power Loss Recovery Feature Auto retract

Bed Auto Leveling

Video tutorial (https://youtu.be/Zoyl6PybsUk)

Most beds appear quite flat and even, but even when the bed is flat, there may be irregularities due to tape or other matter on the surface. Bed Automatic Leveling helps improve the quality of printing and bed adhesion by taking several measurements of the bed surface and then adjusting all movement to follow the tilt or contours of the bed.

Steps of turn on bed auto leveling feature:

If you have not done the auto leveling test before, or you have executed restore defaults, or you have upgraded the firmware, or the auto leveling data is incorrect. You need to redo these steps.

1. Turn on Automatic Bed Leveling on LCD MENU Control>>Configre>>Auto Leveling
2. Do Prepare>>Bed Leveling>>Point 1 ~ Point 4 and adjust the bed mounted screws to level the bed first.
Wait for the hotbed and hotend to cool down if they were not cold before doing this step.
Clean the nozzle, ensure there isn't any filament left on the nozzle.
3. Do Prepare>>Bed Leveling>>Catch Z offset.
4. Do Prepare>>Bed Leveling>>Auto Lebeling. After finished, you will get a "height error table" as below picture.
If the measured values are evenly distributed around 0, and the difference between the
maximum value and the minimum value is less than 0.4 (as shown in Figure 1), we suggest that you do not need to enable the automatic leveling function.
If most of the measured values are bigger than zero and the average value > 0.2 (as shown in Figure 2), please add the Preobe Z offset (new value = previous value + average value of measured (>0) ) and do this steps again.
If most of the measured values are bigger than zero and the average value < -0.2 (as shown in Figure 3), please reduce the Preobe Z offset (new value = previous value + average value of measured (<0>)) and do this steps again.


5. After completing the above steps, the automatic leveling function will be enabled, and then you can start printing the gcode file from SD card. However, when print the first the gcode file, it is possible that the nozzle may be slightly away from the hot bed, you need to double-click the knob to slightly adjust the height between the nozzle and the hot bed, about the steps, please refer to the step 4 of "Print your "Hellow World" works". (https://github.com/ZONESTAR3D/Z9/blob/main/Z9V5/Z9V5-MK6/2.Operation/Operation.md)
6. If you turn off the power of the machine and restart it, you need to turn on the bed automatic leveling function manually, that is, set the value of "Control>>Configre>>Active autolevel:" to ON in the LCD menu.
For a more detailed user manual about bed automatic leveling, please refer to: https://github.com/ZONESTAR3D/Upgrade-kit-guide/blob/main/Bed_Leveling_Sensor/PL-08N/ABL_LCDDWIN.md

Power auto shutdown

Video tutorial. (https://youtu.be/SJLpmJL-tG4)

Turn on the auto shutdown feature on LCD screen

You can turn on the auto shut down feature on LCD sceen, after turned on it, the machine will shut down automatically:

1. In a non printing state, you did not perform any operations through the display knob within 15 minutes.
2. After the SD card printing is completed, the hot bed and hot end issues cool down to below the safe temperature for 15 minutes.


Turn on the printer after print finish by adding command

You can also add a "M81" gcode command in the "End G-code" of the slicing software, it will turn off the printer after finished to print the gcode file.


Auto Mixing Feature

The color mixing feature is a function to mix multi different color filaments and extruded from one nozzle to get a new color filament. By adjusting the extrude ratio of each extruder, it can get different color filament. For example, mix Magenta and Yellow filament as a ratio 5:1 to get Red filament, and mix Magenta and Yellow filament as a ratio 1:1 to get Orange filament, etc..
For details about the Color Mixing Feature, please refer to https://github.com/ZONESTAR3D/Document-and-


User-Guide/blob/master/Mixing_Color/Auto_Mixing.md.

Filament Run Out Detect

Introduction of Filament Run Out Sensor

LED: Filament detection indicator light, it will light up when the filament is inserted. "IN" Connector: Connect to the control board or the previous FROD.
"OUT" Connector: Connect to the next FROD. Let it suspend if there is not the next one. The filament must be inserted in the direction indicated by the arrow.

Wiring diagram of Filament Run Out Sensors


The "Filament Run Out Sensors" (there are 4 pieces for Z9V5Pro) are series connected , it means any one "filament run out" is detected, the printer will pause printing.

Video tutorial (https://youtu.be/QCJ-6L6ze1w)

If there is not enough filaments left in the filament roll to complete the current printing, you can enable the "Runout Sensor" feature. The machine will pause the printing when detected the filament is run out, then you can load a new filament roll and resume the printing. What you need to do is:

1. Pass the filament through the Filament Run Out Sensor.
2. Turn on the run out feature on LCD screen.


Notice

1. If you're sure that the filament is enough, do not pass the filament through the Filament Run Out Sensor.


2. The printing pause may cause some obvious defects on the prints.
3. If you need to use the Filament run out detect function, you should insert filaments on all 4 sensors. If you do not actually use 4 filaments when printing, you can cut a small segment of filaments and insert it into the shortage detection sensor. As shown in the following figure:


Power Loss Recovery

Video tutorial (https://youtu.be/f-PpasByiiE)

If your power supply network has frequent power outages, you can enable the automatic power losss recovery function before start printing. When the power goes out and it resumed, you can press the DC switch to turn on the power of the machine, and then the machine will automatically detect the printing breakpoint and provide you with whether you need to continue printing.

Notice

1. Breakpoints data and gcode files will be stored on the SD, must keep the SD card in socket before turn on the machine.
2. The printing pause may cause some obvious defects on the prints.

Auto retract

The retraction setting is very effective in solving string issues. If you are not satisfied with the retraction parameters you set during slicing, you can enable "Auto Retract" function on the LCD menu. Once Auto Retract is enabled, the retraction parameters of the gcode file in the SD card will be replaced by the parameters in the LCD menu during the printing process, which will help you find the retraction settings suitable for your machine and filamanets.
1. Enter Auto Retract Menu Open the Configure Menu and click Auto Retract to enable


2. Setting parameters if need


1. Turn ON / OFF auto retraction feature.
2. Set retract distance (mm) for each extruder.
3. Set retract speed (mm/s).
4. Set the overload filament length (mm) after each retraction.
5. Set reload speed (mm/s).

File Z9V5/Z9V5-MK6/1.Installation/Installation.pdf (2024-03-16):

Installation.md | 2024-03-16

# Z9V5Pro-MK6 Installation guide

## Installation video tutorial (https://youtu.be/TGHUVzV1Pg4)

## ATTENTION

Please strictly follow the standard operation when installation.

Please put the printer away from the reach of kids.

Must be guided by adults when children are installed or used.

Take care when installation, to avoid electrical shock hazards.

Hotend has high temperature even the printer stop working.

Hotbed has high temperature even the printer stop working.

Please keep well-ventilated condition! May produce toxic gases when printer working.

## Parts list


1. Bottom Assembly | 2. Top Assembly | 3. Controller
Assembly | 4. Hot end assembly
5. Control Panel | 6. Left Z carrier Assembly | 7. Right Z carrier
Assembly | 8. Hotbed
9. Hot bed Bracket | 10. Filament Bracket | 11. Magnetic hotbed
sticker | 12. Hotbed screws /nuts
13. Z-axis Profile | 14. Others (screws, tools, cable tie, SD card, Spare
parts, etc.)

## Before installation

Machine View (after installed)


Installation direction


Pay attention to distinguish the front and back of the top and bottom assembly.

Pay attention to distinguish the left Z carrier assembly and the right Z carrier assembly.

## Assembly

1. Install Z profiles

Install 4 Z Profiles to the bottom assembly. Note that there is a hole on one of side of Z profile, this side should be toward to the upper. There is a hole next to the rubber foot pad of the bottom assembly, which is used to fix the Z-axis profile. Mount M5x22 screws from the bottom profiles upwards and secure to Z profile.


Pay attention to the hole on the Z profiles, it should be put on the top and outside.
2. Install Left & Right Z carriers

Install Left & Right Z carriers to the bottom assembly. Note that the side with a Z limit switch of the Z carrier should towards the back of the machine. Mount M4x18 screws from the bottom profile upwards and secure to the sheet metal of the Z carrier.


Pay attention to distinguish Left Z carrier assembly and Right Z carrier assembly.
3. Install top assembly

Place the top assembly (the side with motors on the back) on the Z-axis profiles, note that the screw cap of the Z carriers should be placed in the groove of the profile of top assembly. Two sides are fixed to the sheet metal of the Z carriers by using M4x36 long screws, use 4 PCS M5x22 screw to fix the top assembly and the Z-axis profiles, and use other 4 PCS M5x22 screws to fix the side of the Z profiles and the Y-axis profiles.

Don't tighten these screws in this step.


4. Install controller assembly

4.1 Put the control box assembly between the top assembly and the top assembly of the back of the machine, use 4 PCS M5x22 screws to fix it on the profiles.

4.2 Tighten all those screws installed on step 3.

4.3 Install the bellows holder to the center of top-back profile.


5. Adjust the eccentric columns

5.1 Adjust the eccentric columns (2 PCS on the left and 2 PCS on the right) under the Y carrier, and move the Y profile from front and back, ensure it can move smoothly and doesn’t shake.

5.2 Adjust the eccentric column under the X carriers, and move the X carriers from left and right, ensure it can move smoothly and doesn’t shake.


6. Install hot bed parts

6.1 Take down these M4 screws first on Z carriers metal pieces and then use these M4 screws to mount hot bed brackets on the Z carriers,

6.2 Install aluminum heat bed to the hot bed brackets, the springs should be placed between the heat bed and the bracket, install the hand nuts under the brackets.

Note the the hotbed cable should be place to the right-back corner of the machine.


7. Install control panel

Install control panel to the center of bottom-front profile.


8. Install filament holders

Install 4 sets of filament brackets to the back Z profiles.


9. Install hotend assembly

Loosen the 3 pcs of screws on the hot end assembly and then mount the hot end assembly to the X carrier.


10. Past the heat bed sticker

Place the "A side" of the magnetic hot bed sticker (that with PC film) on the hot bed (B side has already pasted on the heat bed).

Congratulate!; Wiring Guide Online Document. Wiring Guide pdf file.

Now the machine installation is announced to be completed, next you can arrange to wiring.

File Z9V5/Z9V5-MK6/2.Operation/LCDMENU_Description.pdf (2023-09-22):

LCDMENU_Description.md | 2023-09-22

# LCD Menu Description

## Brief of the Control Panel

Intruduction of menu; Operation of the knob

1. Title bar | 2. Menu bar | 3. Status bar | 4. Control knob
5. Printing Menu | 6. Prepare Menu | 7. Setup Menu | 6. Information Menu

Press: Execute command / Enter menu.
Rotate clockwise: Increase the value / Move to the next menu item.
Rotate anti-clockwise: Decrease the value / Move to the pervious menu item.

## LCD Menu

Main Menu


1. LOGO | 2. Print from SD card | 3. Prepare to print
4. Machine Settings | 5. Machine Information | 6. Nozzle Temperature
7. Hotbed Temperature | 8. Printing Speed | 9. Current Z position

Printing status Menu (Hotend Type is “Non-mixing")

1. Titel | 2. Printing file name and Progress bar
3. Extruder Status and FAN Speed
4. Printed time and Remain time | 5. Set printing parameters
6. Pasue&Resume Printing
6. Stop Printing | 7. Nozzle Temperature
8. Hotbed Temperature
9. Printing Speed | 10. Current Z position
12.Status Message Bar

Printing status Menu (Hotend Type is “Mixing")


1. Titel | 2. Printing file name and Progress bar
3. Extruder Mix Rate and Auto Mixing mode
4. Printed time and Remain time | 5. Set printing parameters
6. Pasue&Resume Printing
6. Stop Printing | 7. Nozzle Temperature
8. Hotbed Temperature
9. Printing Speed | 10. Current Z position
12.Status Message Bar

Prepare Menu


Level 1 | Level 2 | Description
Auto Home | HOME ALL | HOME all axis at once
Auto Home | HOME X | HOME X axis
Auto Home | HOME Y | HOME Y axis
Auto Home | HOME Z | HOME Z axis
Temperature | Nozzle Temp | Set Nozzle(hotend) Temperature
Temperature | Bed Temp | Set Hotbed Temperature
Temperature | Fan Speed | Set Extuder Cooler FAN speed
Temperature | PreHeat PLA | Set Nozzle/Hotbed at once (lower temperature for PLA filament)

Level 1 | Level 2 | Description
Temperature | PreHeat ABS | Set Nozzle/Hotbed at once (lower temperature for ABS filament)
Temperature | Cooldown | Stop heating Hotend and Hotbed at once
Move | X | Move X axis
Move | Y | Move X axis
Move | Z | Move X axis
Move | Extruder(n) | Move Extruders (to feed/unload filament)
Move | Extruder All | Move All Extruders (to feed/unload filament)
Filament | Preheat nozzle | Preheat the nozzle to the setting temperature
Filament | Extruder | Choose which extruder to operate
Filament | Slowly length | How long filament be load/unload while did “Slowly Load" & “lowly Unload”
Filament | Quickly length | How long filament be load/unload while did “Quickly Load" & "Quickly Unload“
Filament | Slowly Load | Load filament slowly
Filament | Slowly UnLoad | Unload filament slowly
Filament | Quickly Load | Load filament quickly
Filament | Quickly UnLoad | Unload filament quickly
Bed Leveling | Point 1 | Do leveling at the bed corner 1
Bed Leveling | Point 2 | Do leveling at the bed corner 2
Bed Leveling | Point 3 | Do leveling at the bed corner 3
Bed Leveling | Point 4 | Do leveling at the bed corner 4
Bed Leveling | Catch Probe Z- offset | Auto Catch the probe Z offset (Display only “Auto levleing" is ON)
Bed Leveling | Adjust the probe Z offset | Auto Catch the probe Z offset (Display only “Auto levleing" is ON)
Bed Leveling | Auto leveling | Do auto leveling measure (Display only “Auto levleing" is ON)
Language | EN/ES/RU/FR/PT | Set menu language
Disable Steppers | | Turn off the power supply to motors
Power off | | Power off the printer


Control Menu

Control Menu Description

Menu 2 | Menu 3 | Description
Mixer* | Mix | Set mix rates of each extruder and commit to V-TOOL

Menu 2 | Menu 3 | Description

Gradient(ON/OFF) Start a Gradient mix printing and set paremeters

| Random (ON/OFF) | Start a Random mix printing and set paremeters
| Current V-TOOL | Set current(working) V-TOOL
Configre | Auto Retract | Set Auto Retraction parameters
| Runout Sensor | Turn ON/OFF filament run out detection feature
| Auto Unload | Auto unload filament when printing is abort (only works on Non-mix color hot end)
| PowerLoss Recovery | Turn ON/OFF Power lost Recovery feature
| Auto Shutdown | Turn ON/OFF idel auto shut down feature
| WiFi | Turn ON/OFF WiFi feature
| WiFi BaudRate | Set WiFi BaudRate (Need restart printer and change the WiFi module BaudRate)
| Hotend Type | Set Hot end types (according to your hot end type)
| Extr. Sequence | Change Extruder Sequence (only work on Non-Mixing Color hotend)
| Home Z offset | Set the Z HOME offset
| Auto Leveling | Turn ON/OFF bed auto leveling feature
| Active Auto Level | Active bed auto leveling correct when printing
| Hotend PID | Set the hotend PID parameters
Motion | Feedrate | Set printing speed limiting parameters
| Acceleration | Set acceleration limiting parameters
| Jerk | Set Jerk parameters
| Step/mm | Set Steps/mm parameters of stepping motors
Preheat PLA | Nozzle Temp | Set nozzle temperaturewhen do “Preheat PLA" on Prepare menu
| Bed Temp | Set Bed temperature when do “Preheat PLA" on Prepare menu
| Fan Speed | Set FAN speed when do “Preheat PLA"o n Prepare menu
| Store Settings | Store above settings
Preheat ABS | Nozzle Temp | Set nozzle temperaturewhen do “Preheat ABS" on Prepare menu
| Bed Temp | Set Bed temperature when do “Preheat ABS" on Prepare menu
| Fan Speed | Set FAN speed when do “Preheat ABS" on Prepare menu

Menu 2 | Menu 3 | Description
| Store Settings | Store above settings
Store Settings | | Save the settings
Load Settings | | Load the settings from NVRAM (maybe it has been changed by Gcode command)
Restore Default | | Reset NVRAM settings to the factory status

*Display only when “Control>> Configure >>Hotend type: mixing" see “Control>>Configure"
Tune Menu

Tune menu only display when printing from SD card.


Tune Menu Description

Menu item | Description
Speed | Set the ratio of printing speed
Flow Rate | Set the flow rate of extruder

Nozzle Temp Set Nozzle temperature

Bed Temp | Set Bed temperature
Fan Speed | Set Extruder FAN Speed
Z Offset | Tune Z offset
Mixer | Set mixer,refer to “Control>> Mixer" Menu (only display while “Hotend type is Mixing")
Configure | Tune ON/OFF parts of configurations features, refer to “Control>> Configure" Menu

How to upgrade firmware of DWIN LCD Screen (https://github.com/ZONESTAR3D/Upgrade-kit-guide/tree/main/TFT-LCD/LCD-DWIN)

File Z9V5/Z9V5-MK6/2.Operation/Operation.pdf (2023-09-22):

Operation.md | 2023-09-22


1 / 2

# Operation guide

Before start printing, you need to level the hot bed (fine tune the distance between the nozzle and the printing platform) and load the filaments into the extruders and hot end.

## Leveling the hot bed

Video Tutorial (https://youtu.be/nxzB7ho1kNo)

For FDM3D printers, the distance between the nozzle and the hot bed is very important when printing the first layer. If the distance is too close, the filaments cannot flow out of the nozzle, and even damage the nozzle and the hot bed. If the distance is too far, the filaments cannot pasted on the hot bed, the next layers cannot be stacked correctly and cause printing fail.

Step 1. Power on the 3d printer and then do “Prepare>>Auto Home>>Home All” on LCD MENU, wait the hotend go to the HOME position.
Step 2. Tighten the hand nuts under the bed to move down the bed to the lowest position (Fig 1).
Step 3. Do “Prepare>> Bed leveling>> Point 1” on control panel(Fig 2), the nozzle will go to the corners of the bed, loosen the hand nuts under the hotbed (Fig 3) and let the nozzle almost touch the hotbed (Fig 4). Continue to do “Point 2/3/4” until all of the 4 corners has been leveled.
Step 4. Repeat Step 3 and do 2 ~ 3 rounds, until all of the four corners at the same height.

## Load filaments

Video Tutorial (https://youtu.be/KZQdL7Rgy1s)

This printer is equipped with four extruders and one 4-IN-1-OUT color mixing hot end. The extruders and the hot end are connected by a filament guide (PTFE tube). Before printing, you need to load all 4 filaments to the extruders and feed them into the bottom of the hot end.

Step 1. Do “Prepare>>Auto Home>>Home All” on control panel, and then do “Prepare>>Temperature>> Preheat PLA”, waiting nozzle temperature reached to 190 ℃ (Fig 1).
Step 2. Use a diagonal pliers to cut off the head of filament (Fig 2), and then press the handle of the extruder#1 and insert filament, push the filament until you can see the filament in the PTFE guide (Fig 3). Rotate the gear of extruder #1 (Fig 4), watch the filament until it entered bottom of the hot end.
Step 3. Using the same method as in step 2 to load the filaments to extruder#2 ~ extruder#4, watch the filaments until them entered the bottom of hot end.

Operation.md | 2023-09-22


2 / 2

Step 4. Slowly rotate the gear of extruder#1 ~ extruder#4 one by one and watch the nozzle, until you can see the filament flowed out from the nozzle(Fig 5).

## Print your "Hellow World"" works

Step 1. Insert the SD card to the SD card socket on the printer (Fig 1).
Step 2. Click “Print” on the control panel and choose “Test gcode\xyz_cube.gcode” (Fig 2), click the knob to start printing.
Step 3. Wait until the hotend and hotbed is reached to the setting temperature (Fig 3), the nozzle will home to the origin position and then move to above of the printing platform and extrude the filament, use a tweezers to remove the outflow filament (Fig 4).
Step 4. When the nozzle moved to the hot bed and start to print, double click the knob on the control panel to open a “Baby steps Z” menu (Fig 5), rotate knob slowly to fine tune the height of printing platform, watch the distance from nozzle to bed, until the distance goes well (Fig 6). Wait the printing finished, you will get your first works (Fig 7). Step 5. Wait the hotbed cool (<=25 degree) (Fig 8), and then remove the printed object from the hotbed (Fig 9).

## Congratulate!

After printed the first works, you have a basic understanding of how the 3d printer works. Next, you can print other test files or slice your own 3D model and use the machine to print it out.
It is recommended that you download and install the slicing software, and read the user guide of the slicing software to know how to use it,for details, please refer to the "Slicing Guide".

Slicing Guide Online Document. (https://github.com/ZONESTAR3D/Z9/tree/main/Z9V5/Z9V5-MK6/4.Slicing) Slicing Guide pdf file.

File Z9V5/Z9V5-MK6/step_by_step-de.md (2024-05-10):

[LCD_MENU]: https://github.com/ZONESTAR3D/Z9/tree/main/Z9V5/Z9V5-MK6/LCDMENU_Description.md
[PRUSA_SLICER]: https://github.com/ZONESTAR3D/Slicing-Guide/tree/master/PrusaSlicer
[VIDEO_POWERON]: https://github.com/ZONESTAR3D/Z9/assets/29502731/02fa8e57-a292-4aa5-bb7b-eaa703e3fc1b
[VIDEO_BEDLEVEL]: https://youtu.be/jNf98S0u2VQ
[VIDEO_LOADFILAMENT]: https://youtu.be/1rr4dXRxKc4
[VIDEO_PRINT1C]: https://youtu.be/NbVy8NjKt_s
[VIDEO_PRINT4C]: https://youtu.be/iddKadfrdjw

----
## <a id="choose-language">:globe_with_meridians: Choose language </a>










----
## Schritt für Schritt Anleitung
Kurz gesagt, von dem Moment an, an dem Sie das Gerät erhalten haben, bis zu dem Moment, an dem Sie Ihre eigene 3D-Modelldatei drucken können, sind insgesamt 5 Schritte erforderlich: **Installation – Nivellieren des Bettes – Laden von Filamenten – Drucken der Test-Gcode-Datei – Schneiden und Drucken Sie Ihre eigene 3D-Datei**.
#### Installation (wie Z9V5-MK5)
(https://www.youtube.com/watch?v=pdr8nLl3T3w)
#### Grundoperationen
(https://www.youtube.com/watch?v=GrCOZ4ADHeA)
#### Mehrfarbendruck
(https://www.youtube.com/watch?v=iddKadfrdjw)

### <a id ="a1">Schritt 1. Installation</a>
- 1.1 **Installation**. Weitere Informationen finden Sie im [:book: **Installationshandbuch**](./1.Installation/Installation.md) und im [:clapper: **Installationsvideo-Tutorial**](https://youtu.be/pdr8nLl3T3w). Schließen Sie die Installation der Maschine ab.
- 1.2 **Verkabelung**. Bei der Verkabelung wird grundsätzlich der Stecker in die entsprechende Steckdose gesteckt. Sie müssen darauf achten, **sicherzustellen, dass die Anschlüsse richtig eingesteckt sind**, insbesondere bei den 2PIN-Docking-Buchsen. Darüber hinaus ist bei der Verkabelung des Druckkopfes (Hot End) zu beachten, dass es mehrere Buchsen gleicher, aber unterschiedlicher Farbe gibt, bitte achten Sie darauf, diese entsprechend der Farbe der Buchse zu stecken.
- 1.3 **Einschalten**. Wenn die Verkabelung abgeschlossen ist, können Sie [:clapper: **Z9V5 einschalten**][VIDEO_POWERON]. Bitte beachten Sie insbesondere, dass der Z9V5 über 2 Netzschalter verfügt. Der eine ist der ***Wechselstromschalter*** (der rote Schalter auf der Rückseite der Maschine) und der andere ist der ***Gleichstromschalter*** (ein runder Druckknopfschalter aus Metall an der Vorderseite des Maschinensteuerkastens). Sie müssen zuerst den AC-Schalter einschalten und dann den DC-Schalter etwa 5 Sekunden lang **drücken und gedrückt halten**, um Z9V5 einzuschalten.
- 1.4 **Einfach testen**. Nach dem Einschalten können Sie das Menü auf dem LCD-Bildschirm bedienen ([:book: **LCD-Menübeschreibung**](./2.Operation/LCDMENU_Description.md)), um zu überprüfen, ob das Gerät normal funktioniert. Normalerweise umfasst dies mehrere Schritte:
   - 1.4.1 **Vorbereiten>>Auto Home>>Home All**. Dieser Schritt dient dazu, den Druckkopf des Geräts zum Ursprung zurückzukehren.
   - 1.4.2 **Vorbereiten>>Temperatur>>PLA vorheizen**. In diesem Schritt wird das heiße Ende überprüft und das heiße Bett kann normal erhitzt werden. Wenn in diesem Schritt die Temperatur der Düse 60 Grad übersteigt, sollten Sie sehen, wie sich ein Lüfter auf der rechten Seite des Druckkopfs (heißes Ende) dreht , das ist der Hot-End-Lüfter.
   - 1.4.3 **Vorbereiten>>Temperatur>>Lüftergeschwindigkeit:**. Nachdem Sie den Knopf gedrückt und die Lüftergeschwindigkeit eingestellt haben (auf 255 eingestellt), sollten Sie nun auch den Lüfter (auf der linken Seite für M4V6-Hotend) hochdrehen können.
   Nachdem diese 3 Schritte grundsätzlich festgestellt wurden, dass die Maschine normal funktioniert, können Sie mit den folgenden Schritten fortfahren. Wenn Sie feststellen, dass ein Teil nicht ordnungsgemäß funktioniert, überprüfen Sie bitte die Verkabelung noch einmal oder lesen Sie [:clapper: **Videoanleitung zum automatischen Testen von Maschinen**](https://youtu.be/Mf92BlmKA0A), um eine automatische Maschine zu testen testen.

### <a id ="a2">Schritt 2. Das Bett nivellieren</a>
Bevor Sie mit dem Drucken beginnen, müssen Sie eine einfache Bettnivellierung durchführen, um die Höhe zwischen der Düse und dem Bett (Druckplattform) einzustellen, damit das Filament gut auf dem Bett haften kann. Weitere Informationen finden Sie unter [:clapper: **Videoanleitung zur Bettnivellierung**][VIDEO_BEDLEVEL].

### <a id ="a3">Schritt 3. Filamente laden</a>
Sehen Sie sich dieses [:clapper: Videoanleitung][VIDEO_LOADFILAMENT] an, um alle 4 Filamente in die Extruder und das heiße Ende zu laden.
#### :warning: ACHTUNG BITTE :warning:
1. **Sie müssen alle 4 Filamente am heißen Ende laden, unabhängig davon, ob Sie ein- oder mehrfarbige 3D-Drucke drucken.**
2. **Stellen Sie sicher, dass die Filamente bis zum unteren Ende des heißen Endes geladen wurden, andernfalls kann es zu einer Blockierung des heißen Endes kommen.**

### <a id ="a4">Schritt 4. Test-Gcode-Datei drucken</a>
FDM-3D-Drucker können nur Gcode-Dateien erkennen. Sie müssen die Gcode-Dateien auf die SD-Karte kopieren, die SD-Karte in den SD-Kartensteckplatz des 3D-Druckers einstecken und dann mit dem Drucken beginnen.
Da es sich beim Z9V5Pro um einen 3D-Drucker mit 4 Extrudern handelt, empfehlen wir Ihnen, ein einfarbiges 3D-Modell und ein 4-Farben-3D-Modell zu drucken, um zu testen, ob die Maschine ordnungsgemäß funktioniert.
#### Drucken Sie einfarbige 3D-Drucke
##### [:clapper: Videoanleitung][VIDEO_PRINT1C]
- **Gcode-Datei vorbereiten**. Suchen Sie die Datei **xyz_cube.gcode** auf Ihrer SD-Karte oder [:arrow_down: klicken Sie hier, um sie herunterzuladen](./3.Test_gcode/xyz_cube.zip), entpacken Sie sie auf Ihrem PC und kopieren Sie dann den **xyz_cube .gcode** auf die SD-Karte übertragen, stecken Sie die SD-Karte in den SD-Anschluss des Geräts.
- **Drucken von SD-Karte**. Bewegen Sie den Cursor auf das Element **Drucken** auf dem LCD-Bildschirm, klicken Sie auf den Knopf und wählen Sie die Datei **xyz_cube** aus. Klicken Sie auf den Knopf, um den Druck zu starten.
- **Düsenhöhe fein einstellen**. Warten Sie, bis sich die Düse und das Heizbett erwärmt haben. Wenn Sie mit dem Drucken der ersten Schicht beginnen, doppelklicken Sie auf den Knopf des LCD-Bildschirms und stellen Sie den Abstand von der Düse zum Bett fein ein (Düse ist etwa 0,4 mm höher als der Aufkleber). Warten Sie, bis der Druckvorgang abgeschlossen ist fertig.
#### Drucken Sie 4-farbige 3D-Drucke
##### [:clapper: Videoanleitung][VIDEO_PRINT4C]
- **Gcode-Datei vorbereiten**. Suchen Sie die Datei **M4_4CTest.gcode** auf Ihrer SD-Karte oder [:arrow_down: klicken Sie hier, um sie herunterzuladen](./3.Test_gcode/M4_4CTest.zip), entpacken Sie sie auf Ihrem PC und kopieren Sie dann die Datei **M4_4CTest .gcode** auf die SD-Karte übertragen, stecken Sie die SD-Karte in den SD-Anschluss des Geräts.
- **Drucken von SD-Karte**. Bewegen Sie den Cursor auf das Element **Drucken** auf dem LCD-Bildschirm, klicken Sie auf den Knopf und wählen Sie die Datei **M4_4CTest**. Klicken Sie auf den Knopf, um den Druck zu starten.
- **Düsenhöhe fein einstellen**. Warten Sie, bis sich die Düse und das Heizbett erwärmt haben. Wenn Sie mit dem Drucken der ersten Schicht beginnen, doppelklicken Sie auf den Knopf des LCD-Bildschirms und stellen Sie den Abstand von der Düse zum Bett fein ein (Düse ist etwa 0,4 mm höher als der Aufkleber). Warten Sie, bis der Druckvorgang abgeschlossen ist fertig.

### <a id ="a5">Schritt 5. Schneiden Sie Ihr eigenes 3D-Modell und drucken Sie es aus</a>
Bevor Sie Ihre eigenen 3D-Modelle drucken, müssen Sie die 3D-Modelldatei (eine Datei im stl/obj/AMF-Format, die [aus dem Internet heruntergeladen wurde] (#a6) oder eine eigene Zeichnung) in eine GCode-Datei konvertieren. Dieser Vorgang wird < genannt u>"**Schneiden**"</u>.
- Zuerst müssen Sie die Slicing-Software herunterladen und auf Ihrem Computer installieren und die Parameter Ihrer Maschine in der Slicing-Software einstellen oder die voreingestellte Datei Ihrer Maschine laden, die vom Hersteller des 3D-Druckers festgelegt wurde.
- Als nächstes müssen Sie die Slicing-Software ausführen und möglicherweise auch einige Parameter entsprechend den Eigenschaften Ihrer 3D-Modelldatei festlegen und dann das Slicing ausführen.
- Nachdem das Schneiden abgeschlossen ist, kopieren Sie die generierte Gcode-Datei auf die SD-Karte und folgen Sie den [:point_right:Schritt 4](#a4), um sie mit Ihrem 3D-Drucker auszudrucken.
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

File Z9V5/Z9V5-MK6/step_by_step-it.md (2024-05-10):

[LCD_MENU]: https://github.com/ZONESTAR3D/Z9/tree/main/Z9V5/Z9V5-MK6/LCDMENU_Description.md
[PRUSA_SLICER]: https://github.com/ZONESTAR3D/Slicing-Guide/tree/master/PrusaSlicer
[VIDEO_POWERON]: https://github.com/ZONESTAR3D/Z9/assets/29502731/02fa8e57-a292-4aa5-bb7b-eaa703e3fc1b
[VIDEO_BEDLEVEL]: https://youtu.be/jNf98S0u2VQ
[VIDEO_LOADFILAMENT]: https://youtu.be/1rr4dXRxKc4
[VIDEO_PRINT1C]: https://youtu.be/NbVy8NjKt_s
[VIDEO_PRINT4C]: https://youtu.be/iddKadfrdjw

----
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

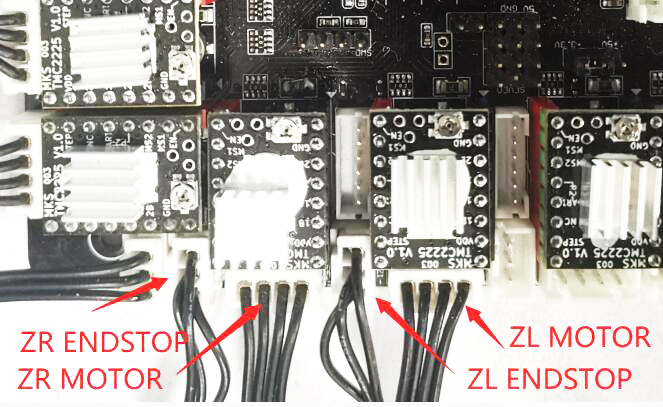
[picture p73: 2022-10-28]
Z9V5/Z9V5_FAQ/Issue_of_Homing/Z_wiring_board.jpg

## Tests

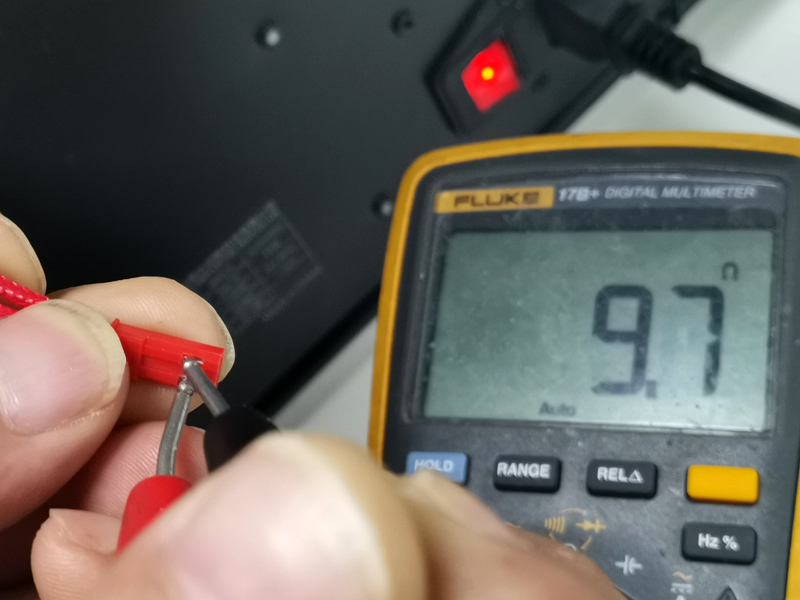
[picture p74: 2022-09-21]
Z9V5/Z9V5_FAQ/Issue_heating/measure.jpg

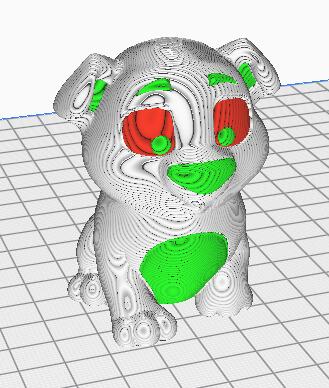
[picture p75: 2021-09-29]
Z9M3/Z9F/3. Test gcode/3 Color/3C_Dog_orig.jpg

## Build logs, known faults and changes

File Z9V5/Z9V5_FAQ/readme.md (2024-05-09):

# Z9V5 Troubleshooting

-----
## Reference
In order to find and solve the problem of the product, you may need to use the automatic test function, open the control box to check the wiring or tune the mortor drive current, use a "swap test" to check an electronic component, etc.. Here we list these guides, pictures and video tutorial for you reference.
### How to open the control box
There are two control boxes on the control backplane of the Z9V5 machine.    
The upper box has the extruder motors and the LED backlight of LOGO inside, and the wires of the shortage detector and the hot end also passes through this box.    
The lower box has control board and AC power socket, and the connectors of X/Y/Z motors, ENDSTOPs and LCD screen is also inside the box.  
- **How to open the upper box** [:art: Picture](./Upper_box_mounted_screws.jpg)  [:clapper: Video](https://github.com/ZONESTAR3D/Z9/assets/29502731/f32b4a1c-f125-46b9-b6c7-f7fa09b943cc) 
- **How to open the control box** [:art: Picture](./How_to_open_the_control_box.jpg) [:clapper: Video](https://github.com/ZONESTAR3D/Z9/assets/29502731/b1a81306-d17e-41e0-80e3-508cc2afe01d) 

### Electronics parts auto testing
##### [:clapper:**Video Tutorial**](https://youtu.be/Mf92BlmKA0A).
The Z9V5Pro machine has builted-in an automatic testing program. You can use this program to determine where the problem comes from when any electronic component encounters a problem.    
To start this program, you need to open the "**Info**" menu and rotate the knob to point to the "**Date: xx-xx-xx**" item, and then press the knob five times. 

### About "swap test"
When we find that there is a functional problem in the machine, and the cause of the problem has multiple possibilities (multiple parts may cause to the same problem), we have the opportunity to use the so-called "**swap test**" to locate the cause of the problem as soon as possible.    
For example, if the left Z-axis motor does not work, the problem may come from the wiring, stepper motor, motor cable, the motor drive module on the control board or the control board. Because there are two sets of Z-axis drive systems in the machine - left Z drive systems nd right Z drive system - which are identical, we can exchange the same parts/components/wire on the left and right sides one by one to confirm where the  problem comes from.    
The parts in the machine that can carry out the exchange test include:
- X/Y motor and limit switch.
- ZL/ZR motor and limit switch
- 4 sets of extruder motors
- Heating tube and temperature sensor of hot bed and hot end.

-----
## Contents
- [**The machine can't start up**](./Issue_of_startup/readme.md)
- [**Homing issue**](./Issue_of_Homing/readme.md)
- [**Stepping motor(s) does not work properly**](./Issue_of_stepping_motor/readme.md)
- [**Heating issue**](./Issue_heating/readme.md)
- [**Not read SD card issue**](./Issue_not_read_sdcard/readme.md)
- [**Bed auto leveling issue**](./Issue_bed_auto_leveling/readme.md)
- [**Auto shut down when printing from SD card**](./Issue_auto_shut_down/readme.md)
- [**Auto pause when printing from SD card**](./Issue_auto_pause/readme.md)
- [**Mixing Color hotend is clogged**](./Issue_mix_color_hotend_clogged/readme.md)
- [**LCD screen knob issue**](#lcd-screen-knob-issue)
- [**Crash when connecting USB in Cura**](./issue_of_connect_USB_in_Cura/readme.md)
<!-- - [**Logo Backlight issue**](./Issue_of_Backlight/readme.md) -->
<!-- - [**Not extruding at the start of the print**](./Issue_not_extrusion_at_start/readme.md) -->
<!-- - [**Prints not sticking to bed**](./Issue_not_sticking_to_bed/readme.md) -->
<!-- - [**Filament run out sensor issue**](./Issue_FROD/readme.md) -->
<!-- - [**Filament clogged issue**](./Issue_M4hotend_clogged/readme.md) -->
<!-- - [**Shifted layers when printing from SD card**]() -->
<!-- - [**Pillowing, e.g. incomplete top layer fills, top layer holes/gaps**]() -->
<!-- - [**Warping or coner lifting**]() -->
<!-- - [**Layer separation or warping within the part**]() -->
<!-- - [**Blobs and/or pimples on exterior surface**]() -->
<!-- - [**How to fix Extruder insufficient discharge issue**](./Issue_of_Extruder_insufficient_discharge/readme.md) -->
<!-- - [**How to improve strings/drawing/oozing issue of the mixing color hotend**](./Issue_of_strings_drawing_m4/How_to_improve_Strings_or_Oozing_issue_of_mixing_color_hotend.pdf) -->
<!-- - [**Scars on top surface**]() -->
<!-- - [**Infill showing on exterior of print**]() -->
<!-- - [**Weak infill**]() -->

-----
## Other references
- **[44 Common 3D Print Problems](https://github.com/ZONESTAR3D/Document-and-User-Guide/tree/master/FAQ)**
- **[All Problems & Solutions (@All3DP.com)](https://all3dp.com/1/common-3d-printing-problems-troubleshooting-3d-printer-issues/)**

-----
## LCD screen knob issue
If you find that the knob of the LCD screen is stuck, you can click on [:gift: this link](https://www.aliexpress.com/item/3256805596235491.html) to purchase a replacement keypad. If your product is within the warranty period (within 12 months from the date of receiving the package), please contact us after placing the order, and we will provide you with after-sales service.     
How to replace the keypad of the LCD screen, please watch the video tutorial:
- For the welding version (older), please refer to [:clapper: this video](https://youtu.be/Xwfczp3nLOY).   
- For the FPC version (newer), please refer to [:clapper: this video](https://youtu.be/z9E6glRZRIQ).  
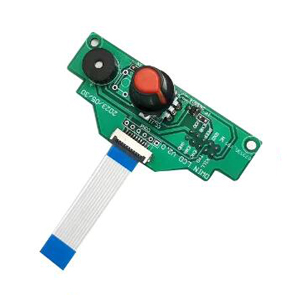
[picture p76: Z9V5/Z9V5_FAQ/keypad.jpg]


-----
## If you can't find a solution to solve your problem after readed the FAQ , please contact our technical support team by email. :email: support@zonestar3d.com .

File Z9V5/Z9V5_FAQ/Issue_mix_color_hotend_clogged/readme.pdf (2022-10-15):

readme.md | 10/15/2022

## How to fix the clogged issue for mixing color hotend

ATTENTION

For the 4-IN-1-OUT color mixing hot end of the 3th version (M4V3) and the 4th version (M4V4) 4-IN-1-OUT hotend, please note the following points:

Use the "hotend-clean-tool" to close the unused channels of hotend before printing. See picture

Don't heating the hot end to over 240℃ if your hotend is the 3th version 4-IN-1-OUT hotend.

Adjust the pressure of the extruder according to the type of filament, especially for the Z9V5Pro. See picture

The PTFE tube connecting the extruder and the hot end shall not be too soft, or it will increase the resistance of filament movement.

When printing multi colors, it is recommended that the printing speed isn't greater than 40mm/s, hot end flow rate isn't greater than 5mm³/s, and the recommended nozzle temperature should be 205℃ (PLA) and 215℃ (PLA+).

NOTE: Default Z9V5-MK1/MK2 equiped with M4V3 hotend, Z9V5-MK3 and Z8P-M4 equiped

Please pay attention to the following points. If these operations are incorrect, the hot end of the heat conduction may be easily blocked

There are many reasons that may cause the hoend to be blocked, please check the list one by one to ensure that you have noticed these matters when using or slicing.

The nozzle are too close to the print platform when printing the first layer.

If the nozzle is too close to the hot bed when printing the first layer, the filament may not be ejected. If this is maintained for a long time, it may cause the filament in the hot end to be over-compressed and cause blockage (often blocked at the entrance of hotend). When printing the first layer, pay attention to the distance between the nozzle and the hot bed. If necessary, open the "BabyStep" menu to adjust the nozzle height.

Slicing settings

For 4-IN-1-OUT mix color hotend, the "Extruder switching retraction length" MUST be set to 0. For example, set “Nozzle Switch Retraction Distance” to 0 when you use Cura Slicer.

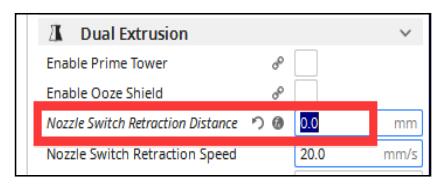
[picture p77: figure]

Filaments loading

When loading the filament to the hotend, please ensure that the filaments enter the bottom of the hot end. If you used less than 4 colors filament, to use the “hotend-clean-tool” to close the unused channels or load filaments to all 4 channels.

Defective nozzle

The nozzle may also be partially clogged. If you find the filament flowed out from the nozzle is thinner than normal, the nozzle may be partially clogged, please replace a new nozzle directly.

How to clean the clogged mix color hotend

Step 1: Heat the hot end (nozzle) to 200℃ and wait for the temperature to be reached
Step 2: Remove the fitting and pull out the filament (Figure 1)

If it is difficult to pull out the filaments, you can use the cutting pliers to clamp the filaments and pull out (Figure 2).
If the filaments cannot be pulled out at all, you can use cutting pliers to cut the filaments.
Step 3: Remove the nozzle from the hot end.

HOT It is recommended to wear heat-resistant gloves for operation.

Step 4: Install the hotend-clean-tool on the hot-end (Figure 3) to close the channels that are not clogged.

If the hot end is blocked by filaments and cannot be inserted into the hotend-clean-tool, you can use a lighter to heat the thin rod of the hotend-clean-tool, and then insert it to the hotend(Figure 4).

Step 5: Manually feed in at least 50cm filaments slowly from the hotend (Figure 5).
Step 6: Clean the filaments in front of the hotend (Figure 6).

If necessary (there are other channels are blocked), you can close the cleaned channel with a “hotendclean-tool” before cleaning the next channel.

Step 7: Install the nozzle back.

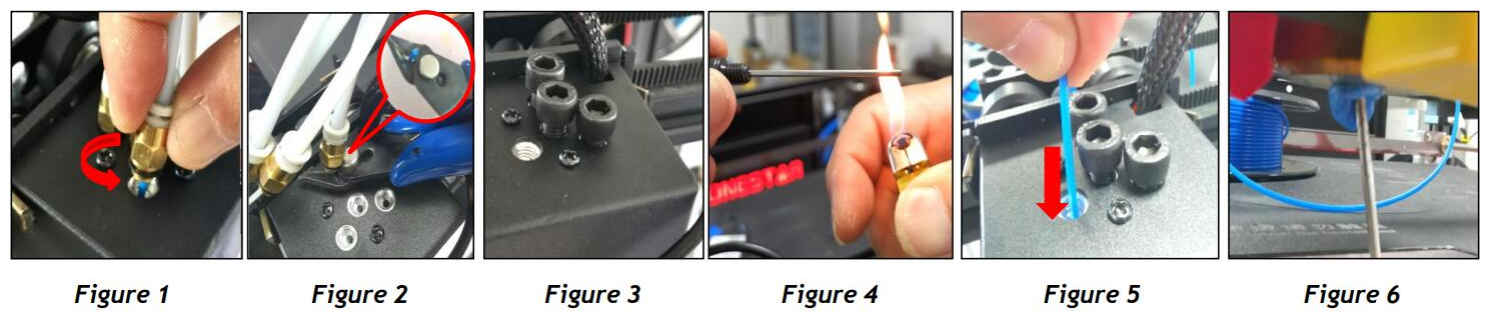
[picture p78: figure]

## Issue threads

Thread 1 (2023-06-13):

Need bed PID tuning

j-snijder, 2023-06-13:
Hi,

As hotend PID tuning is not solving the complete banding problem it would be needed to tune the bed heater PID but thats not in the menu.

Could you please add bed PID tuning to the PID tuning menu options ?

The same way as the hotend {ID is done with an auto tuning function.

And if you want it better then better make it so that on both auto tunings we can choose how many round there should be, 5 rounds is average but if you want a more secure tuning more then 6 would be the way to go, 10 would be the ultimate.

Regards, J. Snijder

Closed 2024-05-10.

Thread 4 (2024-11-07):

print shows that X axis not perpendicular to y axis. 88 degrees instead of 90

dokk179, 2024-11-07:
In the Zonestar Z9V5  I noticed that printing a simple square gives me a Trapezoid (distortions of exactly 2 degrees along the y axis.)
To confirm it I designed a Trapezoid where the y axis line is 2 degrees off and it printed me a perfect square.
I wonder if there is a way to resolve this problem

ZONESTAR3D, 2024-12-12:
The difference in length and tightness between the two belts may cause this issue. You can correct it by following these steps:
Loosen the belt>>Move the X pulley to the rear (easier to handle)>>Adjust and tighten the belt

Closed 2024-12-12.

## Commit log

2021-09-29 add Z9M3
    [3c_test_1.stl, 3c_test_2.stl, 3c_test_3.stl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]
2021-11-17 updata in 2021-11-17
    [Vase.stl]
2021-11-18 add RU/ES/PT/FR/DE user guide
    [Vase.stl]
2021-11-18 updata in 2021-11-18
    [8c_0.stl, 8c_1.stl, 8c_2.stl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]
2021-11-29 updata in 2021-11-29
    [fan_duck_m4_v3.stl]
2021-12-02 updata Z9M4 documents
    [cap_af_20v.stl, fanduck_m4_v3.stl, lcd12864_case_v2.stl]
2021-12-07 updata in 2021-12-07
    [z9_frod_br.stl]
2021-12-10 updata Z9V5 documents
    [8c_0.stl, 8c_1.stl, 8c_2.stl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]
2021-12-17 updata test gcode
    [fanduck_m3_v4.stl]
2021-12-21 updata readme file
    [xyz_cube.3mf]
2021-12-30 add test gcode
    [8c_0.stl, 8c_1.stl, 8c_2.stl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]
2022-01-07 add parts stl
    [FRODV6-A.stl, FRODV6-B.stl, FilamentSpoolBracket_70mm.stl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]
2022-01-07 updata parts stl
    [Recyclebin.stl]
2022-01-20 add How_to_Fix_Extrude_Feeder_Installation_Issue
    [fan_duck_m4_v3.stl]
2022-03-30 update FROD case stl file
    [FRODV6-A.stl, FRODV6-B.stl, FRODV6_A.stl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]
2022-04-20 add Z9V5 weekly updates news
    [fan_duck_m4_v3.stl, fan_duck_m4_v4.stl, z9v5_recyclebin_100.stl]
2022-07-19 updata Z9V5-MK3 bed auto leveling guide
2022-08-12 updata print parts
    [br_zlsensor_v2.stl]
2022-08-30 updata guide
    [8c_0.stl, 8c_1.stl, 8c_2.stl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]
2022-09-08 updata FAQ for Z9V5Pro-MK3
    [fan_duck_m4_v3.stl]
2022-09-12 updata FAQ
    [fan_duck_m4_v3.stl]
2022-09-19 add Z9V5-FAQ
    [fan_duck_m4_v3.stl]
2022-09-21 updata Z9V5 FAQ
    [fan_duck_m4_v3.stl]
2022-12-08 fix wiring diagrame
2022-12-23 update readme of Z9M3
    [3c_test_1.stl, 3c_test_2.stl, 3c_test_3.stl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]
2023-02-28 update readme of FAQ
    [fan_m4v6_v2.stl]
2023-05-23 update FAQ - Heating issue
2023-05-25 updata print_part of Z9V5
    [FRODV6_A.stl, FRODV6_B.stl, FilamentSpoolBracket_70mm.stl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]
2023-08-21 updata document for Z9V5-MK6
    [fanduct_m4v6.stl]
2023-09-22 updata Z9V5Pro-MK6
    [8c_0.stl, 8c_1.stl, 8c_2.stl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]
2023-09-26 updata FROD stl file
2023-10-13 updata readme
    [8c_0.stl, 8c_1.stl, 8c_2.stl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]
2024-03-11 updata fan duct
    [fanduct_4c_v7.stl, fanduct_m4v6.stl]
